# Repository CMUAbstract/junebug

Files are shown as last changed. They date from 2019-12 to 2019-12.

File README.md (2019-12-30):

# Junebug

Junebug is an embedded platform for low-power computing in extreme environments.
It is designed to support intermittent computing and machine learning in outer
space. Junebug is a chipsat or gram-scale satellite development platform.

## Directory Contents

* [components](components/README.md): KiCad component library files
* [datasheets](datasheets/README.md): Component datasheets
* [footprints](footprints/README.md): KiCad component footprint files
* [kicad](kicad/README.md): KiCad project files
* [BOM.csv](bom.csv): Bill of materials
* [NOTES.md](notes.md): Project notes
* [README.md](README.md): This document

## License

Copyright 2019 Bradley Denby

Licensed under the Apache License, Version 2.0 (the "License"); you may not use
this file except in compliance with the License. You may obtain a copy of the
License at <http://www.apache.org/licenses/LICENSE-2.0>.

Unless required by applicable law or agreed to in writing, software distributed
under the License is distributed on an "AS IS" BASIS, WITHOUT WARRANTIES OR
CONDITIONS OF ANY KIND, either express or implied. See the License for the
specific language governing permissions and limitations under the License.

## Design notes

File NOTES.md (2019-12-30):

# Notes for KiCad

* Install the correct version.

```bash
sudo add-apt-repository ppa:js-reynaud/kicad-5.1
sudo apt update
sudo apt install kicad
```

* Open KiCad and choose `File > New > Project...`. Select the project location.
  Un-check "Create a new directory for the project," and type the project name
  (here: `junebug`).

* Launch `Eeschema` (Schematic Layout Editor). Accept "Copy default global
  symbol library table (recommended)." Choose `File > Page Settings...` and
  select "Size: USLetter 8.5x11in"

* Next, open the Symbol Editor by choosing `Tools > Symbol Library Editor` from
  `eeschema`.

* Using the Symbol Editor, choose `File > New Library...`. Enter the project
  name (here: `junebug`), and choose the "Project" scope when prompted.

* Import the BOM symbols provided by `componentsearchengine.com` (free account
  required). Select `File > Import Symbol...` and save in the project library.
  The `.lib` files are provided in the `components/` directory.

* Open the Footprint Editor. Accept "Copy default global footprint library table
  (recommended)." Choose `File > New Library...`. Enter the project name
  (here: `junebug`), and choose the "Project" scope when prompted.

* Open the Footprint Editor and build three custom footprints:
  `MountingHoles_Feather`, `PinSocket_1x16_Feather`, and `PinSocket_6x2_DCMI`.
  See below for details on each custom footprint. Save each footprint in the
  project library. Choose `File > New Footprint...` to get started.

**Feather Mounting Holes**

* Size (x): 3 mm
* Hole size (x): 2.54 mm
* Locations: 1 (-22.86,-8.89), 2 (22.86,-8.89), 3 (-22.86,8.89), 4 (22.86,8.89)
* Labels locations: (0,-12), (0,12)

**Feather Pin Sockets**

* Size (x): 1.54 mm
* Hole size (x): 1 mm
* Locations: 1 (-19.05,0.00), 2 (-16.51,0.00), 3 (-13.97,0.00), 4 (-11.43,0.00),
  5 (-8.89,0.00), 6 (-6.35,0.00), 7 (-3.81,0.00), 8 (-1.27,0.00), 9 (1.27,0.00),
  10 (3.81,0.00), 11 (6.35,0.00), 12 (8.89,0.00), 13 (11.43,0.00),
  14 (13.97,0.00), 15 (16.51,0.00), 16 (19.05,0.00)
* Labels locations: (0,-3), (0,3)

**DCMI Pin Sockets**

* Size (x): 1.54 mm
* Hole size (x): 1 mm
* Locations: 1 (-1.27,-6.35), 2 (1.27,-6.35), 3 (-1.27,-3.81), 4 (1.27,-3.81),
  5 (-1.27,-1.27), 6 (1.27,-1.27), 7 (-1.27,1.27), 8 (1.27,1.27),
  9 (-1.27,3.81), 10 (1.27,3.81), 11 (-1.27,6.35), 12 (1.27,6.35)
* Labels locations: (0,-12), (0,12)

* Import the BOM footprints from `componentsearchengine.com` into the project
  footprint library. Select `File > Import Footprint from KiCad File...` and
  save in the project library. The `.kicad_mod` files are provided in the
  `footprints/` directory.

* Lay out the schematic in `eeschema`. Set the appropriate label values.

* From `eeschema`, select `Tools > Annotate Schematic...` and choose "Use the
  entire schematic;" "Keep existing annotations;" "Sort components by X
  position;" and "Use first free number after 0."

* Also from `eeschema`, choose `Tools > Assign Footprints...` and set the
  footprints.

* Specify footprints that cannot be set automatically:
  `629105150521 : Connector_USB:USB_Micro-B_Wuerth_629105150521`,
  `Conn_01x16 : junebug:PinSocket_1x16_Feather`, and
  `599-0040-007F : junebug:LEDM168X70N`

* Open `pcbnew` (PCB Layout Editor) and choose `File > Page Settings...` to
  select "Size: USLetter 8.5x11in"

* Add the PCB outline with graphic lines and graphic arcs.

**Graphic Lines for PCB Edge**

* (76,78.54) to (76,96.32)
* (78.54,76) to (124.26,76)
* (78.54,98.86) to (124.26,98.86)
* (126.8,78.54) to (126.8,96.32)

**Graphic Arcs for PCB Edge**

Create the following in the Edge.Cuts layer:
* (78.54,78.54) to (78.54,76) with arc angle -90.0
* (124.26,78.54) to (126.8,78.54) with arc angle -90.0
* (78.54,96.32) to (76,96.32) with arc angle -90.0
* (124.26,96.32) to (124.26,98.86) with arc angle -90.0

* Add `MountingHoles_Feather` at (101.4,87.43) and `PinSocket_6x2_DCMI` at
  (124.26,87.43)

* From `eeschema`, choose `Tools > Generate Netlist File...` and select
  "Generate Netlist."

* From `pcbnew`, choose `Tools > Load Netlist...` and browse to the appropriate
  file.

* Place the components, vias, and tracks. The Feather Pin Sockets are placed at
  (101.40,77.10,0.0) and (101.40,97.76,0.0). Other components:
  * J1: (79.50,87.43,-90.0)
  * LEDR1: (79.00,81.50,180.0)
  * LEDY1: (79.00,93.36,180.0)
  * R1: (82.00,80.70,90.0)
  * R2: (82.00,94.16,-90.0)
  * IC4: (85.50,80.80,180.0)
  * IC3: (90.50,80.90,0.0)
  * C1: (84.40,84.90,-90.0)
  * C2: (86.90,84.90,-90.0)
  * C3: (89.40,84.90,-90.0)
  * C4: (91.90,84.90,-90.0)
  * C5: (88.05,91.45,180.0)
  * C6: (96.50,79.80,0.0)
  * C7: (102.50,79.80,0.0)
  * C8: (105.50,79.80,0.0)
  * C9: (102.50,95.20,180.0)
  * C10: (105.50,95.20,180.0)
  * R3: (96.50,95.20,180.0)
  * IC1: (100.00,87.43,180.0)
  * IC2: (111.80,82.00,0.0)
  * Y1: (109.60,87.70,90.0)
  * Y2: (109.40,93.00,90.0)
  * C11: (114.20,86.30,0.0)
  * C12: (114.20,88.80,0.0)
  * C13: (114.20,91.30,0.0)
  * C14: (114.20,93.60,0.0)
  * S1: (119.30,82.80,90.0)
  * S2: (119.30,91.50,90.0)

* Via positions:
  * LEDR: (78.3,81.5)
  * LEDY: (78.3,93.36)
  * Net-(IC1-Pad43): (82.8,89.3)
  * Net-(IC1-Pad45): (83.2,88.4)
  * Net-(IC1-Pad44): (83.6,87.5)
  * EN: (84.5,79.7)
  * LEDR: (85.7,85.2)
  * LEDY: (85.7,87.4)
  * NRST: (86.35,95.8)
  * SWCLK: (87.5,88.2)
  * SWCLK: (87.5,93.7)
  * SWDIO: (88.6,88.2)
  * SWDIO: (88.6,91.2)
  * EN: (89.3,79.7)
  * GND: (89.3,80.9)
  * GND: (89.3,86.3)
  * VUSB: (90.7,84.6)
  * VBAT: (90.7,92.9)
  * NRST: (91.2,95.8)
  * VDD: (91.9,79.7)
  * VDD: (91.9,83.5)
  * GND: (91.9,86.3)
  * VUSB: (92.8,88.2)
  * Net-(IC1-Pad44): (92.8,89.7)
  * SWDIO: (92.8,91.2)
  * 13: (93.8,81.6)
  * VDD: (94.1,92)
  * 12: (94.8,81.6)
  * 13: (95.4,84.2)
  * Net-(IC1-Pad43): (95.4,88.7)
  * Net-(IC1-Pad45): (95.4,89.7)
  * GND: (95.4,90.7)
  * SWCLK: (95.7,93.7)
  * GND: (95.7,95)
  * VDD: (95.8,79.7)
  * 12: (96,83.6)
  * A0: (96,84.8)
  * NRST: (96.3,96.6)
  * A1: (96.6,84.2)
  * GND: (97.2,79.7)
  * 6: (97.2,87.6)
  * MSCK: (97.7,83)
  * 11: (97.9,88.1)
  * MCE: (98.3,79.4)
  * VBAT: (98.4,90.2)
  * 10: (98.6,88.6)
  * MIO0: (98.7,83)
  * A5: (99.3,89.2)
  * A2: (99.3,90.2)
  * SCK: (99.2,94.3)
  * MIO1: (99.8,80.2)
  * A4: (100.2,89.2)
  * A3: (100.2,90.2)
  * MOSI: (100.3,94.3)
  * 4: (100.5,87.6)
  * MIO3: (100.7,80.2)
  * MIO2: (100.9,83)
  * MISO: (101.1,91.9)
  * RX: (101.3,87.2)
  * TX: (102.1,86.8)
  * NRST: (102.2,90.4)
  * TX: (102.38,83)
  * GND: (103.2,79.7)
  * VDD: (103.2,95.1)
  * NRST: (103.4,91.3)
  * A1: (104.6,84.2)
  * SDA: (104.5,87.4)
  * VDD: (104.8,79.7)
  * BOOT: (105,93)
  * TX: (105.8,83)
  * A0: (107.1,84.8)
  * SCL: (107.1,86.3)
  * 5: (107.1,90.9)
  * VDD: (107.2,95.1)
  * MCE: (108.2,79.9)
  * MIO1: (108.2,81.4)
  * MIO2: (108.2,82.9)
  * 6: (110.5,83.9)
  * 11: (111.4,79.9)
  * 11: (111.4,83.9)
  * 10: (112.3,79.9)
  * 10: (112.3,83.9)
  * 5: (113.2,83.9)
  * BOOT: (113.3,96)
  * 4: (114.1,96.6)
  * MIO3: (115.3,81.4)
  * MSCK: (115.3,82.6)
  * MIO0: (115.3,83.9)

* `pcbnew`: `Preferences > Preferences...` Pcbnew Units: Inches

* `pcbnew`: `File > Board Setup...`
  * Design Rules: Prohibit overlapping courtyards
    * Minimum track width: 6.0 mils
    * Minimum via diameter: 20.0 mils
    * Minimum via drill: 10.0 mils
    * Minimum uVia diameter: 20.0 mils
    * Minimum uVia drill: 10.0 mils
    * Minimum hole to hole: 8.0 mils
  * Net Classes (Edit the Default)
    * Clearance: 6.0 mils
    * Track Width: 6.0 mils
    * Via Size: 27.0 mils
    * Via Drill: 13.0 mils
    * uVia Size: 27.0 mils
    * uVia Drill: 13.0 mils
    * dPair Width: 6.0 mils
    * dPair Gap: 6.0 mils
  * Solder Mask/Paste
    * Solder mask clearance: 2.0 mils
    * Solder mask minimum width: 4.0 mils

* `pcbnew`: `Preferences > Preferences...` Pcbnew Units: Millimeters

* `pcbnew`: `Edit > Edit Track & Via Properties...` Set to net class values OK

* Perform design rules check

* Add the text to F.SilkS and B.SilkS: Width 0.4, Height 0.4, Thickness 0.1
* Pin labels (all 0.0 degrees)
  * SWCLK: (82.35,78.4)
  * SWDIO: (84.9,78.4)
  * GND: (87.4,78.4)
  * VIN: (90.0,78.4)
  * VCAP: (92.5,78.4)
  * EN: (95.1,78.4)
  * VUSB: (97.6,78.4)
  * 13: (100.1,78.4)
  * 12: (102.7,78.4)
  * 11: (105.2,78.4)
  * 10: (107.8,78.4)
  * 9: (110.3,78.4)
  * 6: (112.8,78.4)
  * 5: (115.4,78.4)
  * SCL: (117.9,78.4)
  * SDA: (120.5,78.4)
  * NRST: (82.35,96.46)
  * 3V3: (84.9,96.46)
  * AREF: (87.4,96.46)
  * GND: (90.0,96.46)
  * A0: (92.5,96.46)
  * A1: (95.1,96.46)
  * A2: (97.6,96.46)
  * A3: (100.1,96.46)
  * A4: (102.7,96.46)
  * A5: (105.2,96.46)
  * SCK: (107.8,96.46)
  * MOSI: (110.3,96.46)
  * MISO: (112.8,96.46)
  * RX: (115.4,96.46)
  * TX: (117.9,96.46)
  * 4: (120.5,96.46)
* Part labels:
  * LEDR: (76.8,81.5,90.0)
  * LEDY: (76.8,93.36,90.0)
  * J1: (78.8,87.43,0.0)
  * R1: (80.8,79.9,90.0)
  * R2: (80.8,94.46,90.0)
  * C1: (84.4,84.6,0.0)
  * IC4: (85.5,79.4,0.0)
  * C2: (86.9,84.6,0.0)
  * C5: (88.05,91.45,0.0)
  * C3: (89.4,84.6,0.0)
  * IC3: (91.75,80.9,0.0)
  * C4: (91.9,84.6,0.0)
  * C6: (94.8,79.8,90.0)
  * R3: (94.8,95.2,90.0)
  * IC1: (100.0,87.43,0.0)
  * C7: (100.8,79.8,90.0)
  * C9: (100.8,95.2,90.0)
  * C8: (105.5,81.0,0.0)
  * C10: (105.5,94.0.0.0)
  * Y2: (109.4,93.0,0.0)
  * Y1: (109.6,87.6,0.0)
  * IC2: (111.8,82.0,0.0)
  * C11: (113.8,86.3,90.0)
  * C12: (113.8,88.8,90.0)
  * C13: (113.8,91.3,90.0)
  * C14: (113.8,93.6,90.0)
  * S1: (119.3,82.8,0.0)
  * S2: (119.3,91.5,0.0)

* Add logo information (try `http://img2mod.wayneandlayne.com`)

* Export the Gerber and Drill files
  (see `https://docs.oshpark.com/design-tools/kicad/generating-kicad-gerbers/`)
  * Select `File > Plot...` and provide an output directory
  * Choose the following layers: `F.Cu`, `B.Cu`, `F.SilkS`, `B.SilkS`, `F.Mask`,
    `B.Mask`, and `Edge.Cuts`; also `F.Paste` and `B.Paste`
  * Check "Exclude PCB Edge from other layers;" check "Use Protel filename
    extensions"
  * Select `Plot`
  * Select `Generate Drill File`
  * Check "Decimal Format;" uncheck "Mirror Y Axis;" check "Merge PTH and NPTH
    Holes into one file"
  * Select `Drill File`

## License

Copyright 2019 Bradley Denby

Licensed under the Apache License, Version 2.0 (the "License"); you may not use
this file except in compliance with the License. You may obtain a copy of the
License at <http://www.apache.org/licenses/LICENSE-2.0>.

Unless required by applicable law or agreed to in writing, software distributed
under the License is distributed on an "AS IS" BASIS, WITHOUT WARRANTIES OR
CONDITIONS OF ANY KIND, either express or implied. See the License for the
specific language governing permissions and limitations under the License.

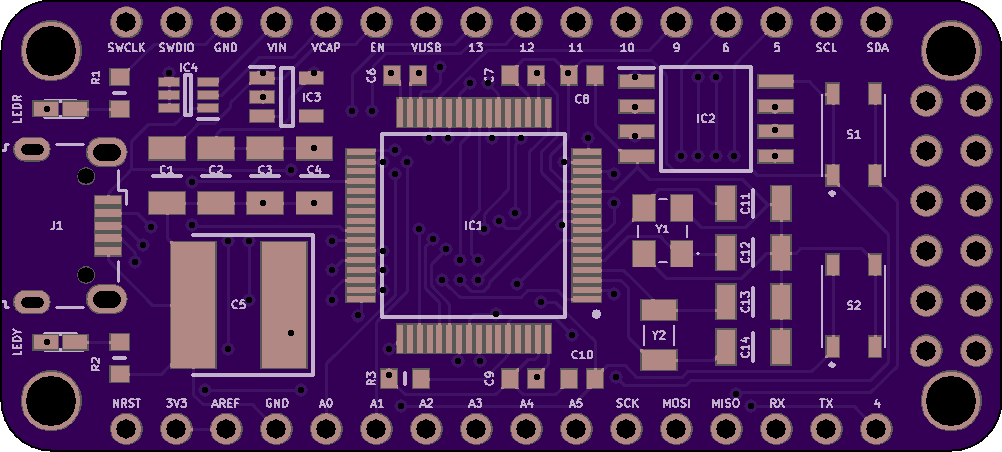
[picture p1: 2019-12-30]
images/junebug-front.png

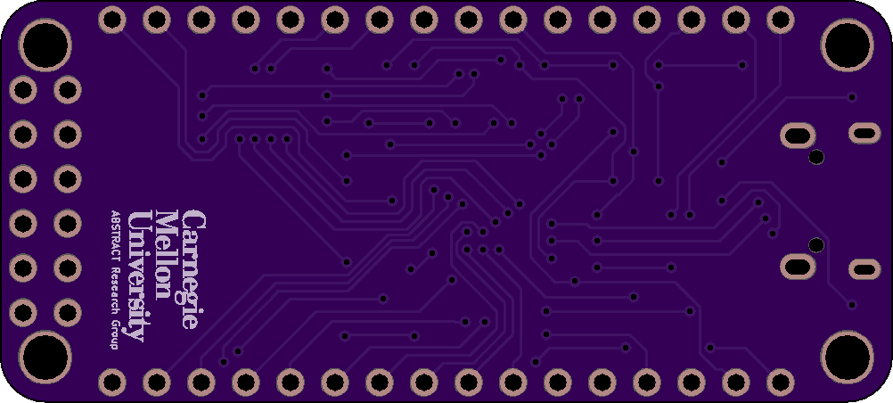
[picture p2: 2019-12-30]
images/junebug-back.png

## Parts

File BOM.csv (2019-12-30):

label | count | id | mouser | url | note | description
IC1 | 1 | STM32L496RGT3 | 511-STM32L496RGT3 | https://componentsearchengine.com/ga/part.php?partID=770355 |  | ARM Cortex M4; 32 bit; 80 MHz; 1 MB program memory; 320 kB data RAM; 12 bit ADC; 52 I/O; 1.71 V to 3.6 V; -40 C to +125 C
IC2 | 1 | IS25LP128F-JBLA3 | 870-IS25LP128F-JBLA3 | https://componentsearchengine.com/ga/part.php?partID=1153919 | Stocked version | NOR flash; 128 Mbit; 133 MHz; SPI; 13.5 mA supply current; -40 C to +125 C
IC3 | 1 | TPS7A0533PDBVR | 595-TPS7A0533PDBVR | https://componentsearchengine.com/ga/part.php?partID=1325310 |  | LDO; 1.4 V to 5.5 V in; 3.3 V out; 200 mA out; 1 uA quiescent current; -40 C to +125 C
IC4 | 1 | MMBD4148TW-7-F | 621-MMBD4148TW-7-F | https://componentsearchengine.com/ga/part.php?partID=297000 |  | Triple diode; peak reverse volt. 80 V; max. surge current 4 A; forward current 500 mA; recovery time 4 ns; forward voltage 1.25 V; reverse current 100 nA; -65 C to +150 C
Y1 | 1 | ABM8AIG-16.000MHz-12-2Z-T | 815-ABM8AIG16122ZT | https://componentsearchengine.com/ga/part.php?partID=1712653 |  | 12 pF; 16 MHz; 20 PPM tolerance; 50 PPM frequency stability; 10 uW drive level; -40 C to +125 C
Y2 | 1 | ABS07AIG-32.768kHz-T | 815-S07AIG-32.768T | https://componentsearchengine.com/ga/part.php?partID=631062 |  | 12.5 pF; 32.768 kHz; 20 PPM tolerance; 100 nW drive level; -40 C to +125 C
C1;C2;C3 | 3 | CC1206JKX7R9BB105 | 603-CC1206JK7R9BB105 | https://componentsearchengine.com/ga/part.php?partID=1609580 |  | Caps for MCU and LDO; 1 uF; 50 V; 5% tolerance; case code 3216 mm; -55 C to +125 C; X7R
C4 | 1 | CC1206KKX7R7BB475 | 603-CC126KKX7R7BB475 | https://componentsearchengine.com/ga/part.php?partID=1798972 |  | Cap for MCU; 4.7 uF; 16 V; 10% tolerance; case code 3216 mm; -55 C to +125 C; X7R
C5 | 1 | 597D158X9004R2T | 71-597D158X9004R2T | https://componentsearchengine.com/ga/part.php?partID=398104 |  | 1500 uF; 4 VDC; 10% tolerance; 15 mOhm ESR; 60 uA leakage current; -55 C to +125 C
C6;C7;C8;C9;C10 | 5 | CC0603JPX7R9BB104 | 603-CC0603JPX79BB104 | https://componentsearchengine.com/ga/part.php?partID=1949354 |  | Caps for MCU; 0.1 uF; 50 V; 5% tolerance; case code 1608 mm; -55 C to +125 C; X7R
C11;C12;C13;C14 | 4 | CC1206CRNPO9BN4R7 | 603-C1206CRNPO9BN4R7 | https://componentsearchengine.com/ga/part.php?partID=1178080 |  | Caps for Xtals; 4.7 pF; 50 V; 0.25 pF tolerance (5%); case code 3216 mm; -55 C to +125 C; C0G(NPO)
R1;R2 | 2 | RT0603FRD07100RL | 603-RT0603FRD07100RL | https://componentsearchengine.com/ga/part.php?partID=2222716 |  | Resistors for LEDs; 100 Ohm; 1/10 W; 1% tolerance; 25 PPM/C; 75 V; case code 1608 mm; -55 C to +155 C
R3 | 1 | RT0603FRD0710KL | 603-RT0603FRD0710KL | https://componentsearchengine.com/ga/part.php?partID=2223925 |  | Resistor for switch; 10 kOhm; 1/10 W; 1% tolerance; 25 PPM/C; 75 V; case code 1608 mm; -55 C to +155 C
LEDR | 1 | 599-0010-007F | 645-599-0010-007F | https://componentsearchengine.com/ga/part.php?partID=1524640 |  | Bootloader user LED; Red 633 nm; 45 mcd; 140 deg; clear lens; forward current 20 mA; forward voltage 2.1 V; -40 C to +100 C
LEDY | 1 | 599-0040-007F | 645-599-0040-007F | https://componentsearchengine.com/ga/part.php?partID=1524642 | Do not use URL model footprint; use LEDR footprint | Charge indicator LED; Yellow 590 nm; 105 mcd; 140 deg; clear lens; forward current 20 mA; forward voltage 2.1 V; -40 C to +100 C
J1 | 1 | 629105150521 | 710-629105150521 | KiCad Connector_USB:USB_Micro-B_Wuerth_629105150521 | Use provided .lib file; Use KiCad footprint | Micro USB type B; female; USB 2.0; 5 contact; 1 port; 3 A; horizontal mounting angle
S1;S2 | 2 | PTS810SJM250SMTRLFS | 611-PTS810SJM250SMTR | https://componentsearchengine.com/ga/part.php?partID=830194 |  | Tactile switch; non-illuminated; oval; OFF - (ON); straight; 1.6 N; 50 mA; 16 VDC; -40 C to +85 C

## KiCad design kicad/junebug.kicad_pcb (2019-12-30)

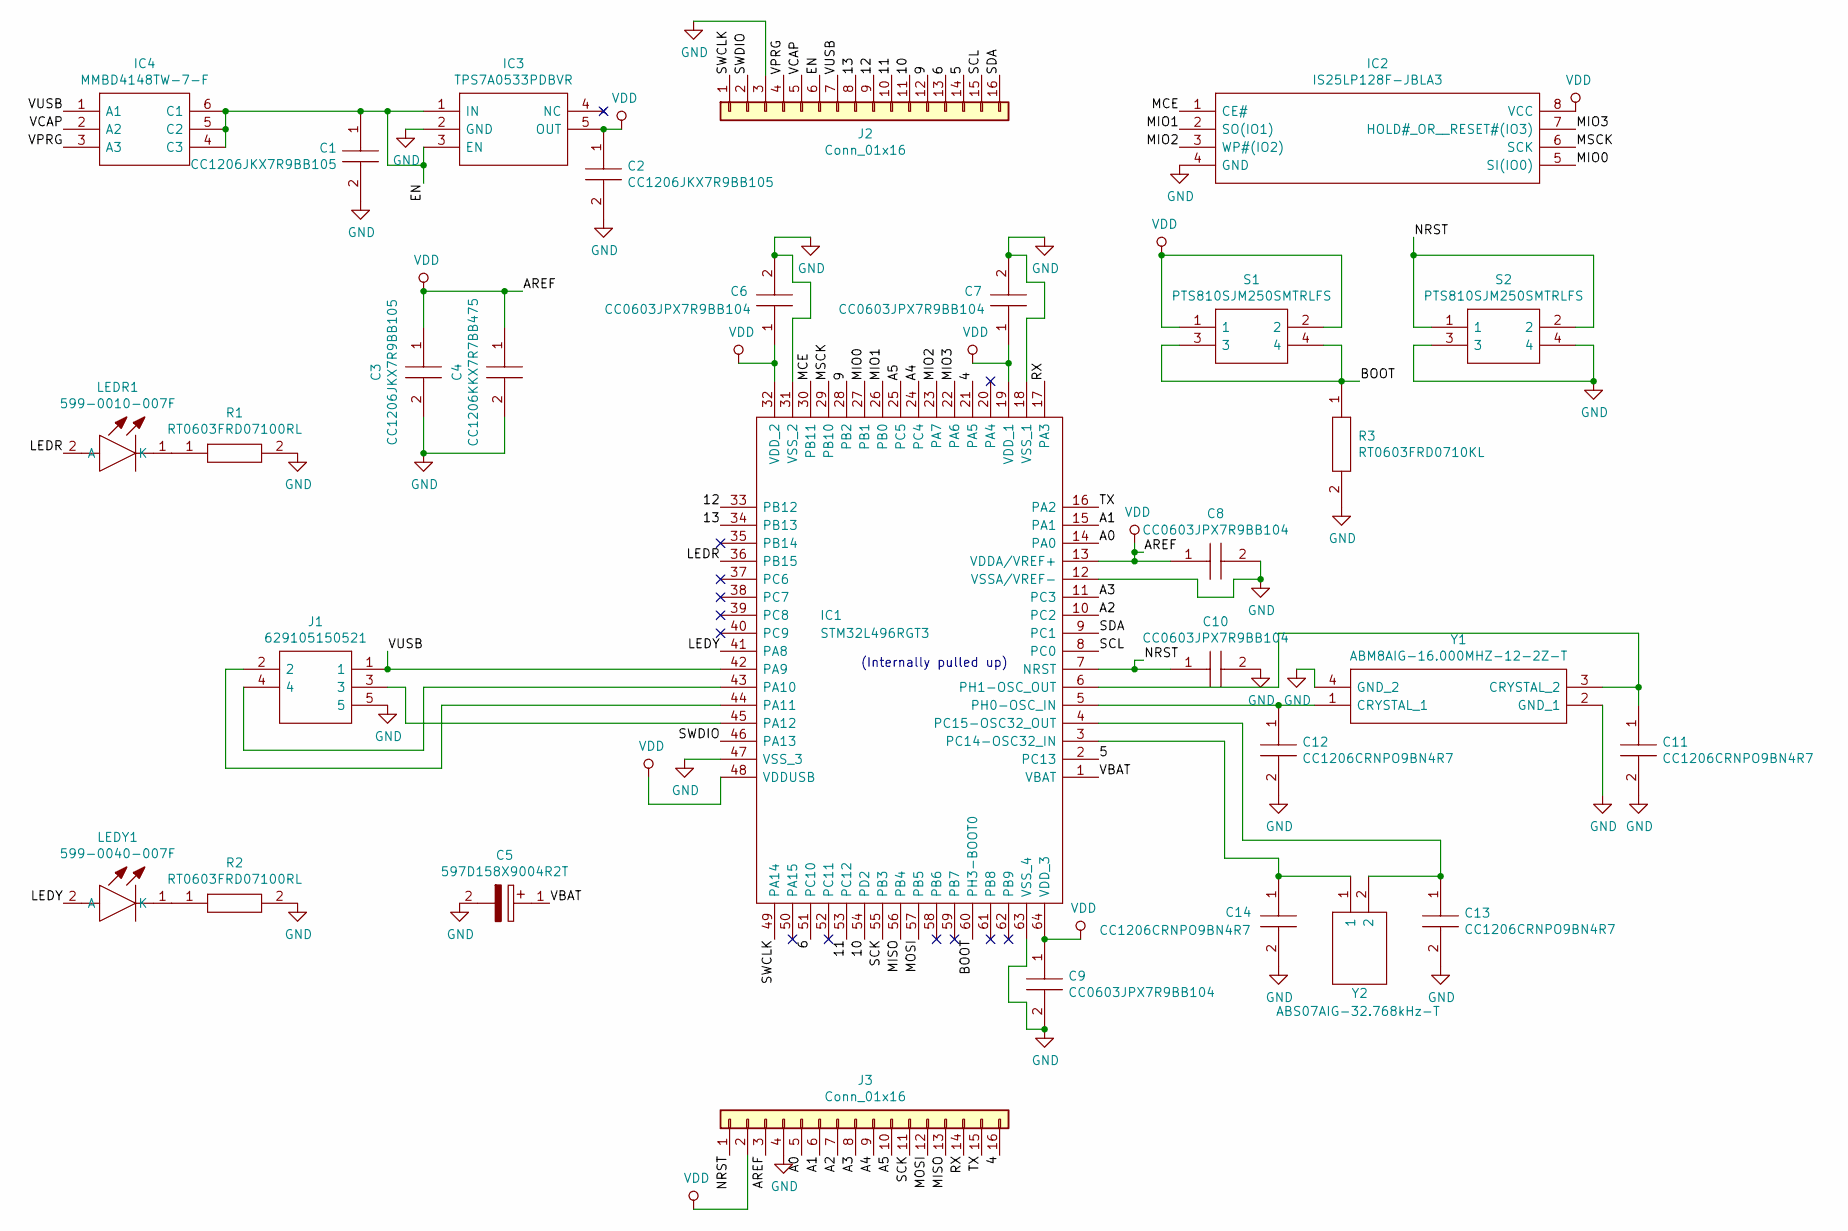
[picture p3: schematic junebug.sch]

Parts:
C1, C2, C3: CC1206JKX7R9BB105; CAPC3216X180N; Manufacturer_Part_Number CC1206JKX7R9BB105; Mouser Part Number 603-CC1206JK7R9BB105
C4: CC1206KKX7R7BB475; CAPC3216X180N; Manufacturer_Part_Number CC1206KKX7R7BB475; Mouser Part Number 603-CC126KKX7R7BB475
C5: 597D158X9004R2T; Manufacturer_Part_Number 597D158X9004R2T; Mouser Part Number 71-597D158X9004R2T
C6, C7, C8, C9, C10: CC0603JPX7R9BB104; CAPC1608X90N; Manufacturer_Part_Number CC0603JPX7R9BB104; Mouser Part Number 603-CC0603JPX79BB104
C11, C12, C13, C14: CC1206CRNPO9BN4R7; CAPC3216X70N; Manufacturer_Part_Number CC1206CRNPO9BN4R7; Mouser Part Number 603-C1206CRNPO9BN4R7
IC1: STM32L496RGT3; QFP50P1200X1200X160-64N; Manufacturer_Part_Number STM32L496RGT3; Mouser Part Number 511-STM32L496RGT3
IC2: IS25LP128F-JBLA3; SOIC127P790X216-8N; Manufacturer_Part_Number IS25LP128F-JBLA3; Mouser Part Number 870-IS25LP128F-JBLA3
IC3: TPS7A0533PDBVR; SOT95P280X145-5N; Manufacturer_Part_Number TPS7A0533PDBVR; Mouser Part Number 595-TPS7A0533PDBVR
IC4: MMBD4148TW-7-F; SOT65P210X110-6N; Manufacturer_Part_Number MMBD4148TW-7-F; Mouser Part Number 621-MMBD4148TW-7-F
J1: 629105150521; USB_Micro-B_Wuerth_629105150521; Manufacturer_Part_Number 629105150521; Mouser Part Number 710-629105150521
J2, J3: Conn_01x16; PinSocket_1x16_Feather
LEDR1: 599-0010-007F; LEDM168X70N; Manufacturer_Part_Number 599-0010-007F; Mouser Part Number 645-599-0010-007F
LEDY1: 599-0040-007F; LEDM168X70N; Manufacturer_Part_Number 599-0040-007F; Mouser Part Number 645-599-0040-007F
R1, R2: RT0603FRD07100RL; RESC1608X55N; Manufacturer_Part_Number RT0603FRD07100RL; Mouser Part Number 603-RT0603FRD07100RL
R3: RT0603FRD0710KL; RESC1608X55N; Manufacturer_Part_Number RT0603FRD0710KL; Mouser Part Number 603-RT0603FRD0710KL
S1, S2: PTS810SJM250SMTRLFS; PTS810SJG250SMTRLFS; Manufacturer_Part_Number PTS810SJM250SMTRLFS; Mouser Part Number 611-PTS810SJM250SMTR
Y1: ABM8AIG-16.000MHZ-12-2Z-T; ABM8AIG25000MHZ122ZT3; Manufacturer_Part_Number ABM8AIG-16.000MHZ-12-2Z-T; Mouser Part Number 815-ABM8AIG16122ZT
Y2: ABS07AIG-32.768kHz-T; ABS07AIG32768kHz71T; Manufacturer_Part_Number ABS07AIG-32.768kHz-T; Mouser Part Number 815-S07AIG-32.768T

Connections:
/4: IC1.21 (PA5), J3.16
/5: IC1.2 (PC13), J2.14
/6: IC1.51 (PC10), J2.13
/9: IC1.28 (PB2), J2.12
/10: IC1.54 (PD2), J2.11
/11: IC1.53 (PC12), J2.10
/12: IC1.33 (PB12), J2.9
/13: IC1.34 (PB13), J2.8
/A0: IC1.14 (PA0), J3.5
/A1: IC1.15 (PA1), J3.6
/A2: IC1.10 (PC2), J3.7
/A3: IC1.11 (PC3), J3.8
/A4: IC1.24 (PC4), J3.9
/A5: IC1.25 (PC5), J3.10
/BOOT: IC1.60 (PH3-BOOT0), R3.1, S1.3, S1.4
/EN: C1.1, IC3.1 (IN), IC3.3 (EN), IC4.4 (C3), IC4.5 (C2), IC4.6 (C1), J2.6
/LEDR: IC1.36 (PB15), LEDR1.2 (A)
/LEDY: IC1.41 (PA8), LEDY1.2 (A)
/MCE: IC1.30 (PB11), IC2.1 (CE#)
/MIO0: IC1.27 (PB1), IC2.5 (SI(IO0))
/MIO1: IC1.26 (PB0), IC2.2 (SO(IO1))
/MIO2: IC1.23 (PA7), IC2.3 (WP#(IO2))
/MIO3: IC1.22 (PA6), IC2.7 (HOLD#_OR__RESET#(IO3))
/MISO: IC1.56 (PB4), J3.13
/MOSI: IC1.57 (PB5), J3.12
/MSCK: IC1.29 (PB10), IC2.6 (SCK)
/NRST: C10.1, IC1.7 (NRST), J3.1, S2.1, S2.2
/RX: IC1.17 (PA3), J3.14
/SCK: IC1.55 (PB3), J3.11
/SCL: IC1.8 (PC0), J2.15
/SDA: IC1.9 (PC1), J2.16
/SWCLK: IC1.49 (PA14), J2.1
/SWDIO: IC1.46 (PA13), J2.2
/TX: IC1.16 (PA2), J3.15
/VBAT: C5.1, IC1.1 (VBAT)
/VCAP: IC4.2 (A2), J2.5
/VPRG: IC4.3 (A3), J2.4
/VUSB: IC1.42 (PA9), IC4.1 (A1), J1.1, J2.7
GND: C1.2, C2.2, C3.2, C4.2, C5.2, C6.2, C7.2, C8.2, C9.2, C10.2, C11.2, C12.2, C13.2, C14.2, IC1.12 (VSSA/VREF-), IC1.18 (VSS_1), IC1.31 (VSS_2), IC1.47 (VSS_3), IC1.63 (VSS_4), IC2.4 (GND), IC3.2 (GND), J1.5, J2.3, J3.4, R1.2, R2.2, R3.2, S2.3, S2.4, Y1.2 (GND_1), Y1.4 (GND_2)
unnamed: C11.1, IC1.6 (PH1-OSC_OUT), Y1.3 (CRYSTAL_2)
unnamed: C12.1, IC1.5 (PH0-OSC_IN), Y1.1 (CRYSTAL_1)
unnamed: C13.1, IC1.4 (PC15-OSC32_OUT), Y2.2
unnamed: C14.1, IC1.3 (PC14-OSC32_IN), Y2.1
unnamed: IC1.43 (PA10), J1.4
unnamed: IC1.44 (PA11), J1.2
unnamed: IC1.45 (PA12), J1.3
unnamed: LEDR1.1 (K), R1.1
unnamed: LEDY1.1 (K), R2.1
VDD: C2.1, C3.1, C4.1, C6.1, C7.1, C8.1, C9.1, IC1.13 (VDDA/VREF+), IC1.19 (VDD_1), IC1.32 (VDD_2), IC1.48 (VDDUSB), IC1.64 (VDD_3), IC2.8 (VCC), IC3.5 (OUT), J3.2, J3.3, S1.1, S1.2

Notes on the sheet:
(Internally pulled up)

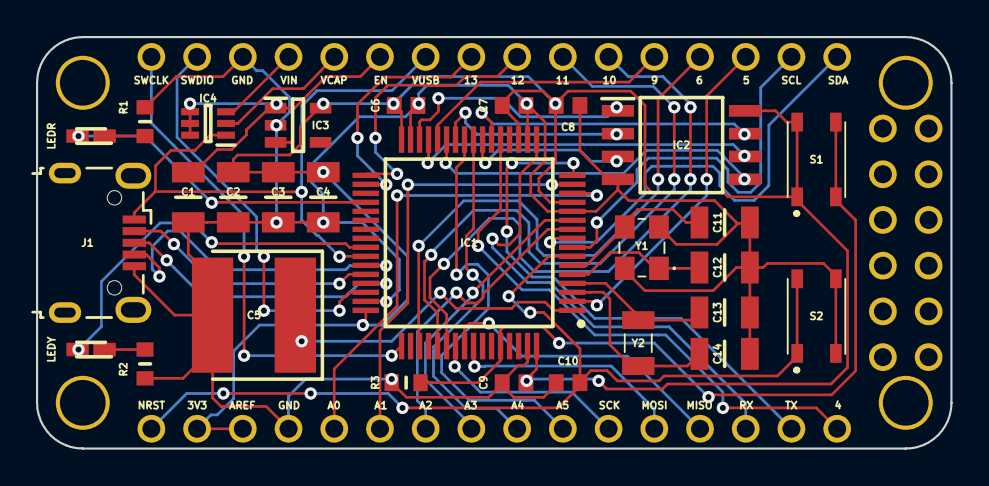
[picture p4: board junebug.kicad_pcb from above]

Board: 2 copper layers, 50.8 x 22.9 mm, 31 parts (1 on the bottom side), 49 nets.

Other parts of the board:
cmu-logo: cmu-logo
